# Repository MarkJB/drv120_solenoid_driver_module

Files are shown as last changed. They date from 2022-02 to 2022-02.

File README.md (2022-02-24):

# drv120_solenoid_driver_module

A small PCB module for efficiently driving a solenoid.

Rev B

Originally designed for use with drawing machines for fast up/down pen control but applicable to any project that involves driving a DC solenoid (as a guide > ~30 ohms). A TI DRV120 chip drives the solenoid with a configurable PWM frequency and takes care of the initial fast energize required to get the solenoid moving then ramps down the current to a lower level to hold the solenoid in place. Peak & keep (hold) current and PWM frequency are configurable with resistors and caps (see schematic and data sheet). 

Testing with the chosen solenoid (MCSMO-0603S12STD) resulted in using a 4.7uF capacitor for C1 (KEEP), 47K ohm resistor for R1 (PEAK) and a 0 ohm resisitor for R2 (OSC) for the default PWM frequency value (~20kHz).

See [datasheet](http://www.ti.com/lit/ds/symlink/drv120.pdf) for more details.

Rev B uses JST PH 2.00mm headers. If you are looking for a decent crimper that doesn't cost the earth, I can reccomend the [IWISS SN-2549](https://www.amazon.co.uk/gp/product/B01N4L8QMW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), available on Amazon for a lot less than the offical crimps. The litte extra jaws that jut out at the front do a decent job of crimping these small connectors.

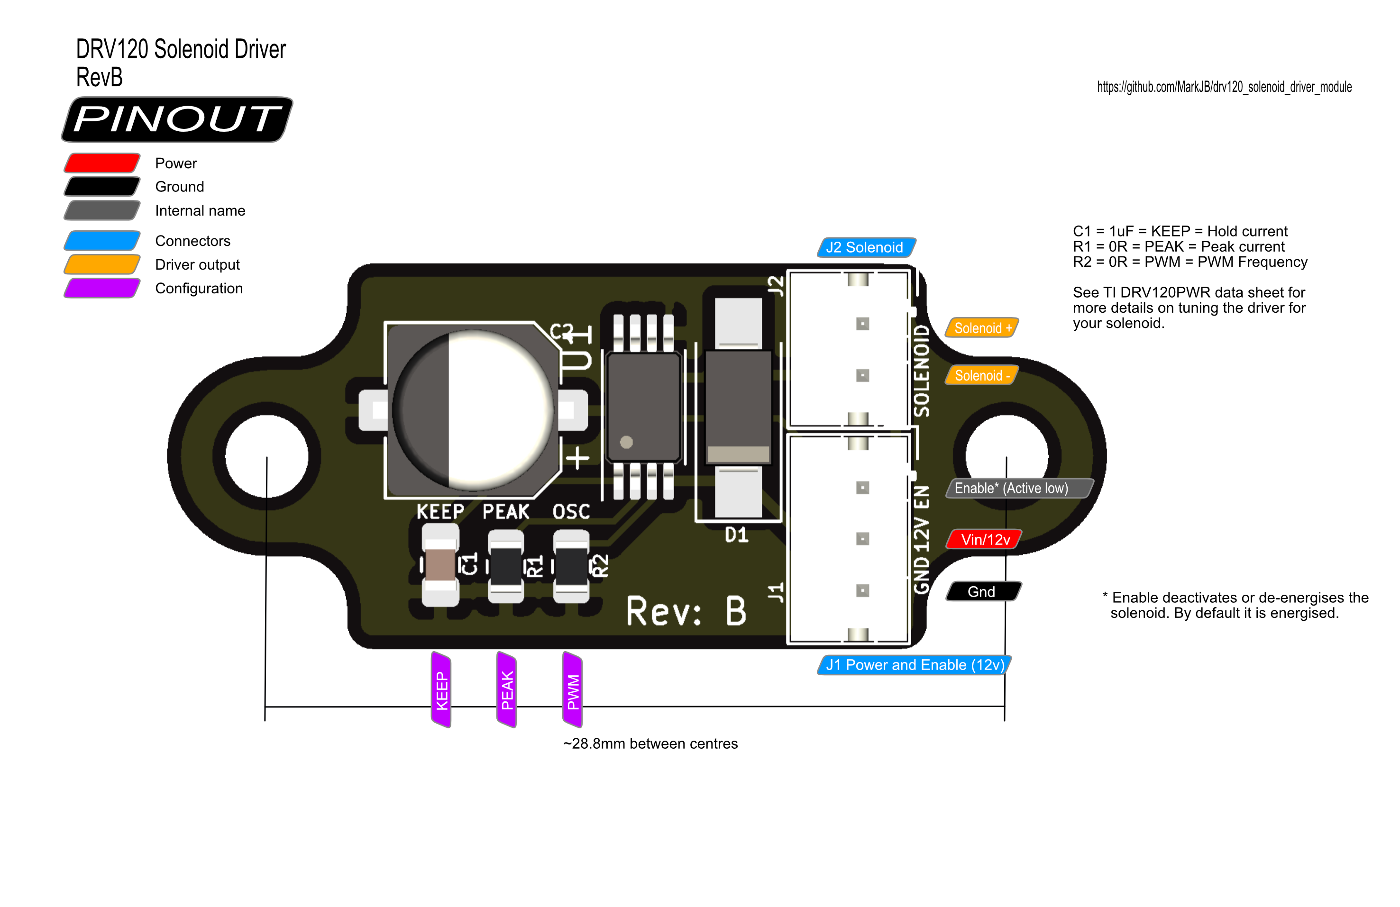
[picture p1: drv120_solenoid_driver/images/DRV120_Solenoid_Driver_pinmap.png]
Pinmap


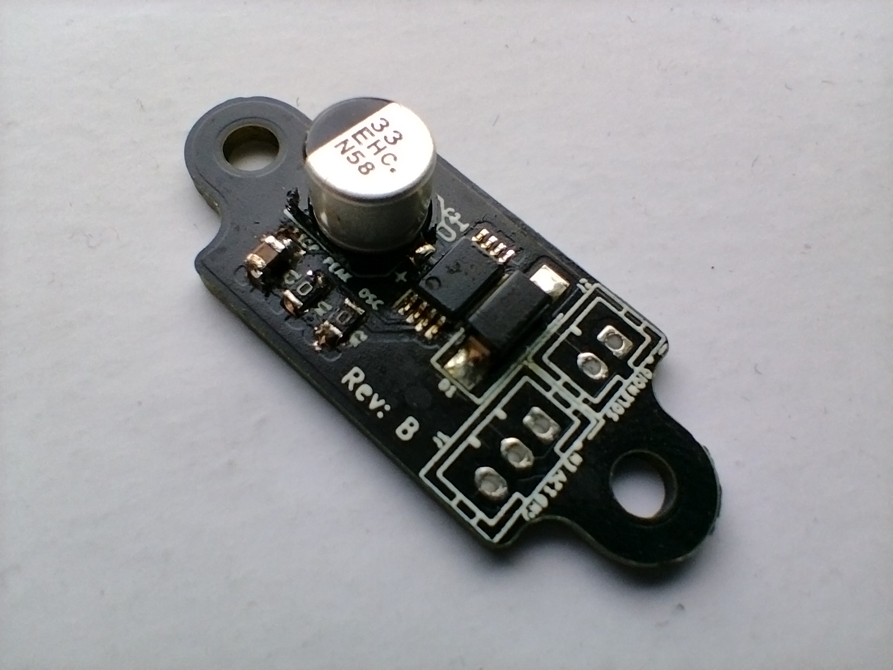
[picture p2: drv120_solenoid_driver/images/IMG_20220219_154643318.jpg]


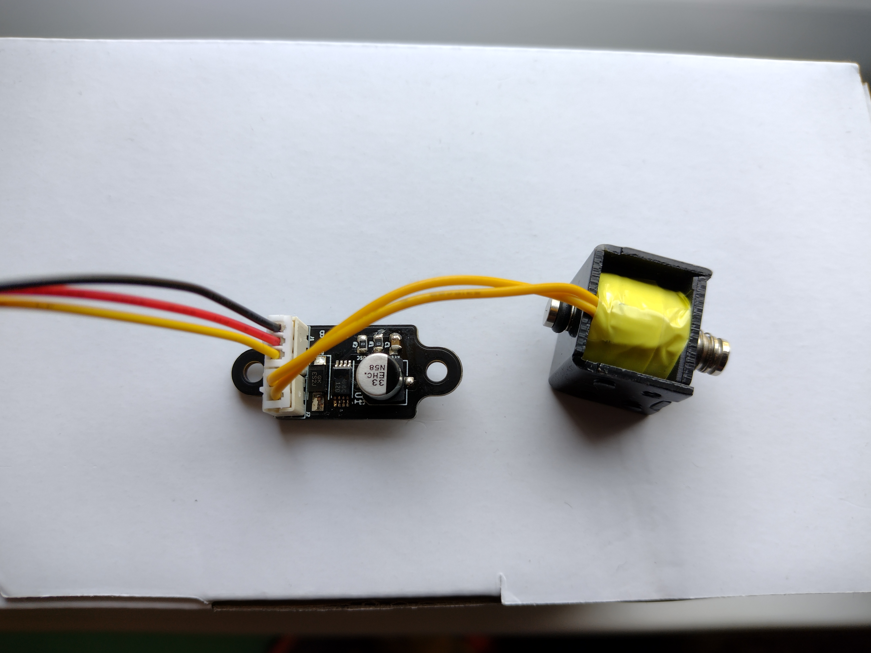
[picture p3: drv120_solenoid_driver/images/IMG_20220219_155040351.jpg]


# Buy a board
Buy from my [tindie store](https://www.tindie.com/products/edit/solenoid-driver-module-drv120-pwm-dc-6-24v/)

# Make a donation
If you find this project useful, consider donating.



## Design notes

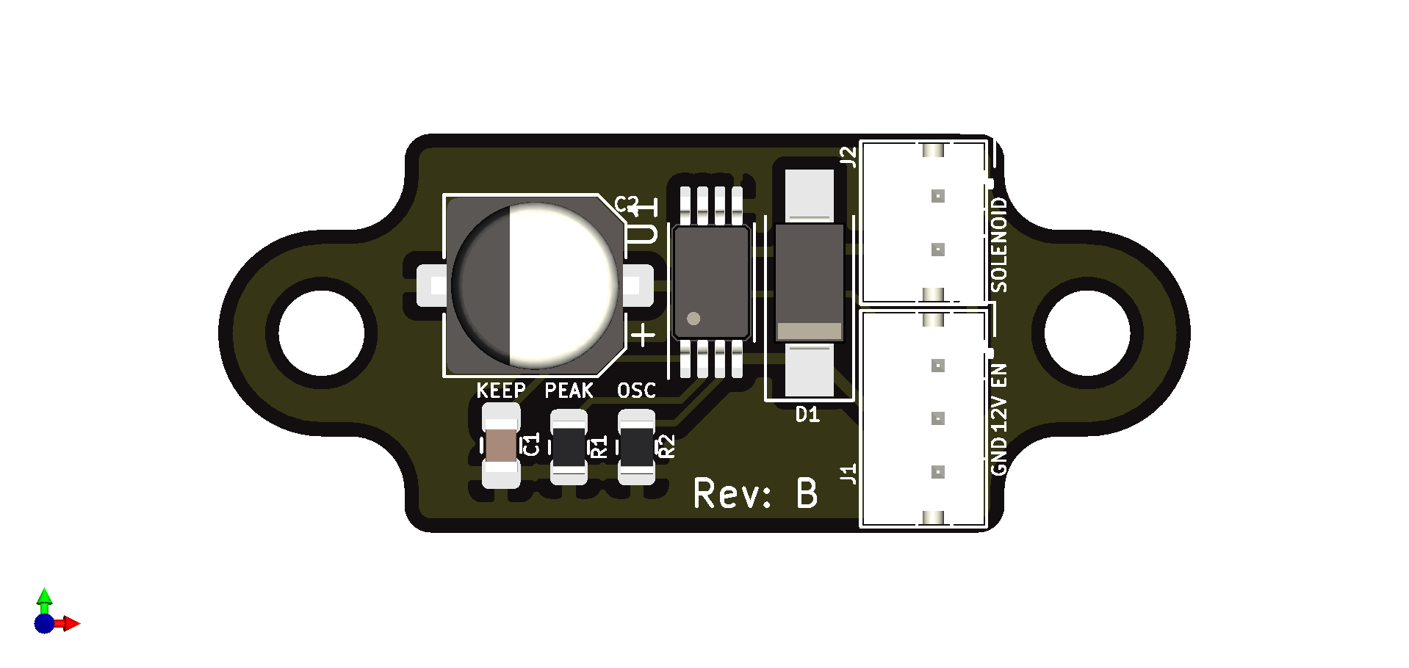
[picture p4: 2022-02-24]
drv120_solenoid_driver/images/drv120_solenoid_driver_top_projection.png

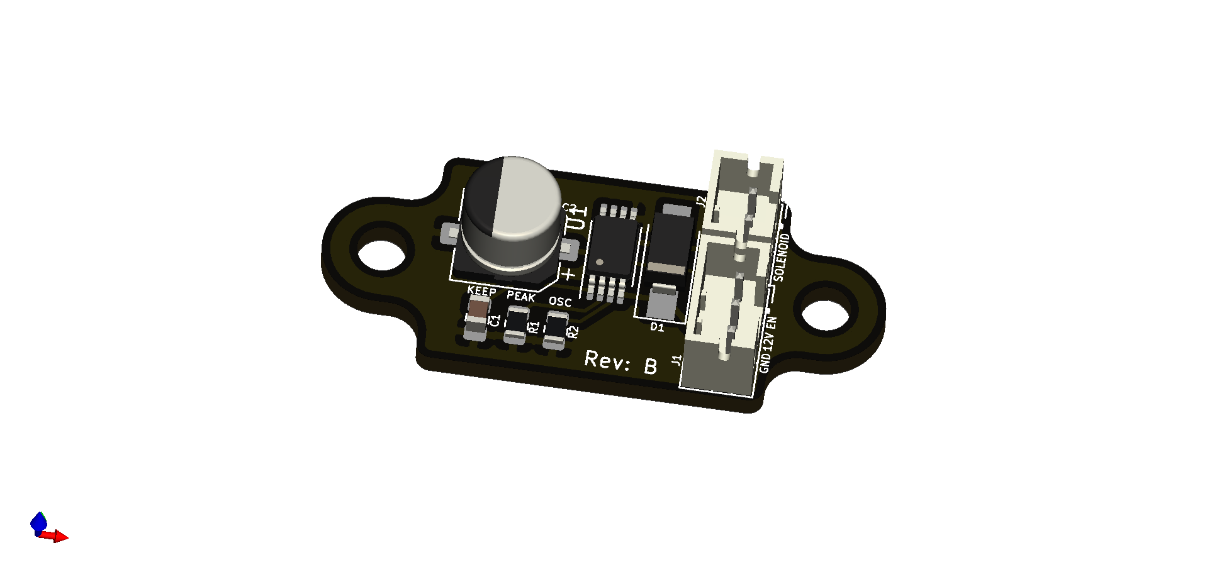
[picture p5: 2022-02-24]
drv120_solenoid_driver/images/drv120_solenoid_driver.png

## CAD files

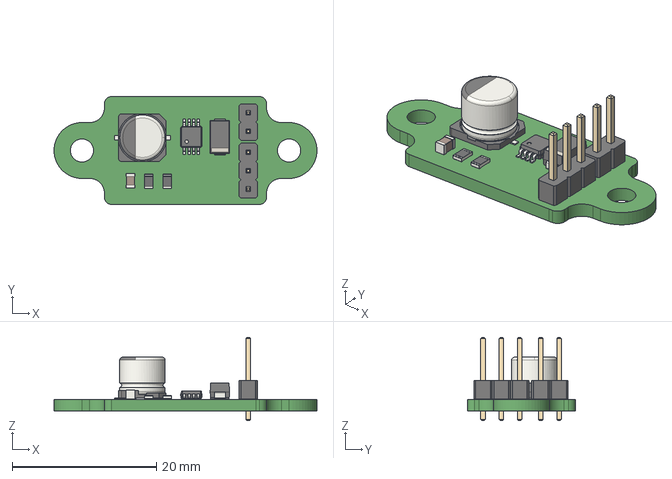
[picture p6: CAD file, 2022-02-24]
drv120_solenoid_driver/drv120_solenoid_driver.step
36.4 x 15.0 x 11.5 mm

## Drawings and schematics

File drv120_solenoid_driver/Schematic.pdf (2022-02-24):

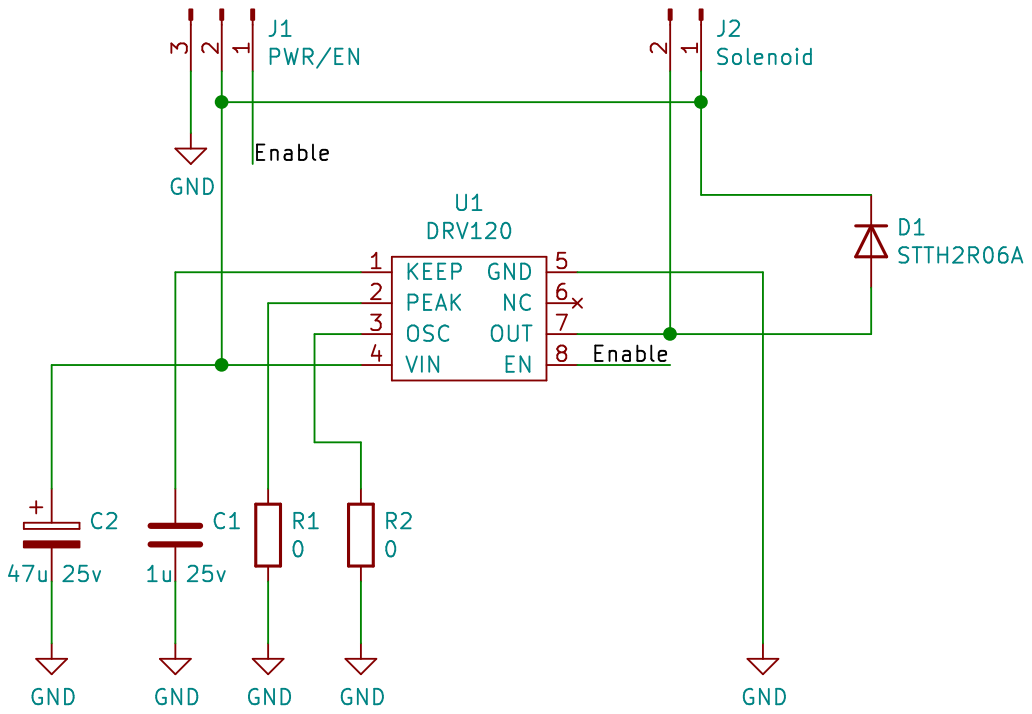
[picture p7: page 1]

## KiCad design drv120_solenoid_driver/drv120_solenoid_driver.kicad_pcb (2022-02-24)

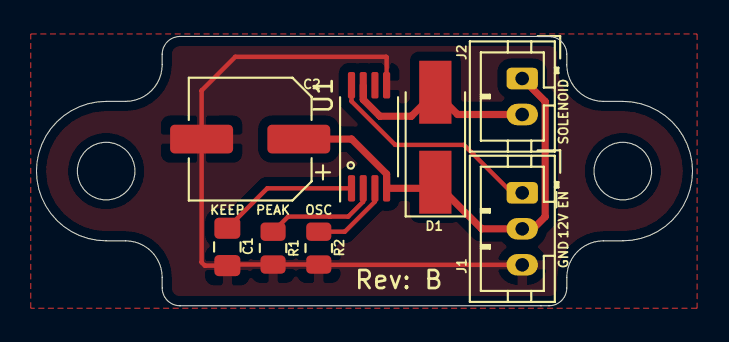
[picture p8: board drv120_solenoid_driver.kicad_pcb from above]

Board: 2 copper layers, 36.4 x 15.0 mm, 8 parts (0 on the bottom side), 7 nets.

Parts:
C1: 1u; C_0805_2012Metric_Pad1.18x1.45mm_HandSolder
C2: 47u; CP_Elec_6.3x5.8
D1: D; D_SMA_Handsoldering
J1: PWR/EN; JST_PH_B3B-PH-K_1x03_P2.00mm_Vertical
J2: Solenoid; JST_PH_B2B-PH-K_1x02_P2.00mm_Vertical
R1, R2: 0; R_0805_2012Metric
U1: drv120; TSSOP-8_4.4x3mm_P0.65mm

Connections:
/Enable: J1.1, U1.8
GND: C1.2, C2.2, J1.3, R1.2, R2.2, U1.5
unnamed: C1.1, U1.1
unnamed: C2.1, D1.1, J1.2, J2.1, U1.4
unnamed: D1.2, J2.2, U1.7
unnamed: R1.1, U1.2
unnamed: R2.1, U1.3

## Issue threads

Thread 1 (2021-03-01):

Add mounting holes

MarkJB, 2021-03-01:
Really need hardware mounting points.

MarkJB, 2022-02-24:
Fixed in RevB

Closed 2022-02-24.

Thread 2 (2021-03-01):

Rework input pins

MarkJB, 2021-03-01:
Having two 2 pin inputs allows flexibility but is unnecessary in practice. Make this one single 3 pin connector.

MarkJB, 2022-02-24:
Fixed in RevB

Closed 2022-02-24.

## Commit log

2020-02-25 Single sided PCB
    First pass at a single sided PCB
    [drv120_solenoid_driver.kicad_pcb, drv120_solenoid_driver.sch]
2020-02-26 Single sided for engraver
    [drv120_solenoid_driver.kicad_pcb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]
2020-03-19 Double sided PCB v0.2
    [drv120_solenoid_driver.kicad_pcb]
2020-03-20 Updated silk screen around connectors
    [drv120_solenoid_driver.kicad_pcb]
2020-05-01 Add photo of prototype boards
    [drv120_solenoid_driver-B_Cu.gbl, drv120_solenoid_driver-B_Mask.gbs, drv120_solenoid_driver-B_SilkS.gbo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]
2020-05-01 Add PDF of schematic
2021-10-21 Tab mounting version
    PCB design with mounting tabs on either side
    [drv120_solenoid_driver.kicad_pcb, drv120_solenoid_driver.step]
2021-10-26 Changed to JST-PH 2.00 TH connectors
    Also changed input connector to a single 3 pin JST. Solenoid is on a 2 pin JST.
    [drv120_solenoid_driver.kicad_pcb, drv120_solenoid_driver.sch]
2021-10-26 Add production files
    [drv120_solenoid_driver-B_Cu.gbl, drv120_solenoid_driver-B_Mask.gbs, drv120_solenoid_driver-B_Paste.gbp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]
2021-11-10 Add component part numbers
    [drv120_solenoid_driver.sch]
2022-02-24 Add pin map, new images, schematic pdf and clean up old files
2022-02-24 Add tindie store link and paypal donation button
2022-02-24 Use shareable link/hosted button for paypal donate button.
2022-02-24 Clean up
    [drv120_solenoid_driver.sch]
